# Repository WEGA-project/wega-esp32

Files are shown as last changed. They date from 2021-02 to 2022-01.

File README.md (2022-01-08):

# Важно !!!
**Данный репозиторий не актуален, используйте прошивку из [wegabox](https://github.com/WEGA-project/wegabox)**

*****

# WEGA-ESP32

Web Electronic Garden Automatic on ESP32 project.

Телеграмм канал проекта [WEGA-ESP32](https://t.me/esp32wega)

И так, что же такое **WEGA-ESP32(WEGA-Box)**

**WEGA-ESP32** это система контроля и мониторинга состояния гидропонной системы, куда входят следущие возможности
* Мониторинг `ЕС`
* Мониторинг `pH`
* Мониторинг `Температуры воздуха и раствора`(в баке и в корневой зоне)
* Мониторинг `Влажности воздуха`
* Мониторинг `Освещенности`
* Мониторинг `Уровня раствора`
* Управление корневым давление(на сколько это возможно)
* Контроль `ЕС` в рабочем баке(в разработке, дата релиза не известна)

Важно: **WEGA-ESP32(WEGA-Box)** не имеет смысла без [WEGA](https://github.com/WEGA-project/WEGA/wiki) части.

Так же **WEGA-ESP32** является важным звеном в [WEGA ecosystem](https://github.com/WEGA-project/WEGA-Mixer/blob/main/images/wega-ecosystem.jpg)

Содержание 
=================
<!--ts-->
* [Минимальные требования и знания](#what_to_know)
* [Схема подключения компонентов](#schema)
* [Что потребуется купить(ESP32, датчики, резисторы)](#what_to_buy)
<!-- * [PCB плата](#pcb) -->
* [Установка софта](#install)
  * [Arduino IDE](#arduino)
  * [Additional Boards Manager URLs](#boards_manager)
  * [Установка платы ESP32](#esp_board_install)
  * [Visual Studio Code configuration](#vscode)
* [Залив прошивки esp32wega](#esp_wega)
* [Компоненты для модуля измерения pH](#ph)
* [Корпуса для 3D печати](#3d)
* [Распиновка jack](#jack)
* [Калибровка EC](#ec)
* [Где искать помощь](#help)

<!--te-->

### Минимальные требования и знания

Для того, чтобы собрать этот миксер необходимо:

- Минимальные знания в электронике (знать что такое `+` или `GND`)
- Умение читать схему, да-да, именно читать, а не разглядывать и смотреть
- Знание, что такое паяльник и как с ним работать
- Понимание как соединить три проводка в одной точке
- Умение собирать компоненты по схеме
- Знать и уметь, как прошивать ардуину и вообще знать, что это такое
- Минимальные знания в программировании. Мы попытались минимизировать необходимость ковыряние в коде, но все же придется изменять некоторые значения, о которых речь пойдет ниже

Если, всего выше перечисленного или одного из выше перечисленного не знаешь, не умеешь, не понимаешь, найди человека, который соберет этот миксер за тебя.

## Схема подключения
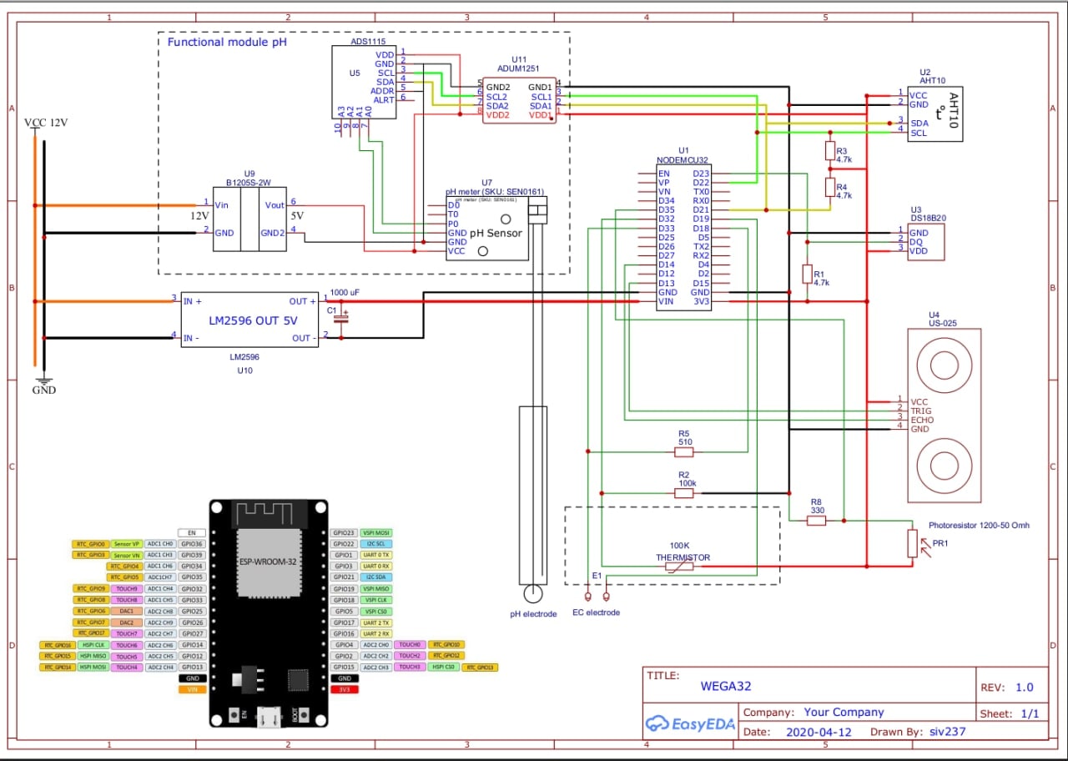
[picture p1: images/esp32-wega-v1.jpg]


## Компоненты для заказа
 1. Плата контроллера [ESP32-WROOM-32D или ESP32-WROOM-32U](https://www.aliexpress.com/wholesale?&SearchText=ESP32-WROOM-32D+ESP32-WROOM-32U+)
 1. Датчик температуры и влажности [ATH10](https://aliexpress.ru/wholesale?SearchText=AHT10). [Пример позиции](https://aliexpress.ru/item/4000961263862.html)
 1. Фоторезистор [GL5528](https://aliexpress.ru/wholesale?SearchText=GL5528) для измерения света. [Пример позиции](https://aliexpress.ru/item/1125719348.html)
 1. Датчик расстояния для измерения уровня [US-025](https://www.aliexpress.com/wholesale?&SearchText=Ultrasonic+Ranging+Module+US-025)
 1. Стабилизатор для питания контроллера [mini560 5V](https://aliexpress.ru/wholesale?&SearchText=mini560+step+down+5V)
 1. Терморезистор 100кОм для компенсации ЕС [NTC-MF52-100K](https://www.aliexpress.com/wholesale?&SearchText=Thermistor+Resistor+NTC-MF52-100K). [Пример позиции](https://aliexpress.ru/item/32865194243.html)
 1. Водонепроницаемый [ds18b20](https://www.aliexpress.com/wholesale?&SearchText=ds18b20+waterproof) датчик температуры корней. [Пример позиции](https://aliexpress.ru/item/32832225749.html)
 1. [Монтажная плата](https://aliexpress.ru/item/32546265487.html) или [такая](https://www.aliexpress.com/item/32512415633.html)
 1. Набор резисторов [Resistor Assorted Kit Set 10 -1M ](https://www.aliexpress.com/wholesale?&SearchText=Resistor+Assorted+Kit+Set+10+-1M+). [Пример позиции](https://www.aliexpress.com/item/1005002275520555.html)
 1. Провода ...

<!-- 

#### PCB плата
PCB плата находится в стадии активной разработки и тестирования, по этому если планируете заказать плату то иммейте ввиду, что нет ни какой гарантий,
что все будет работать как надо.

PCB плата [WEGA-ESP32](https://oshwlab.com/siv237/esp32wega4)

<a href="images/pcb-esp32-wega.png"><img src="images/pcb-esp32-wega.png" width="250"></a> 
-->

### Установка софта(Install software)

#### Arduino IDE
[Install Arduino IDE](https://www.arduino.cc/en/software)

Запускаем Arduino IDE, прописываем путь к `Additional Boards Manager URLs` для нашей ESP, устанавливаем нашу плату(board)

**Additional Boards Manager URLs**

File -> Preferences

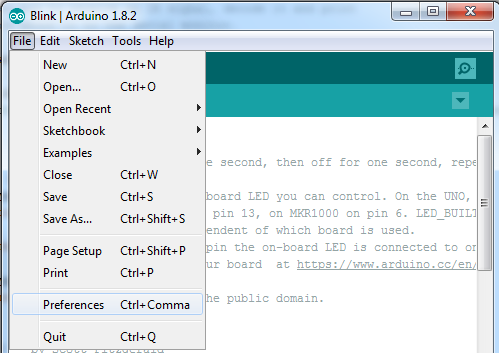
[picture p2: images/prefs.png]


И здесь нам надо изменить две вещи.

1. Необходимо указать расположение вашей папки с esp32 проектом/скетчами, где находятся файлы ардуины.

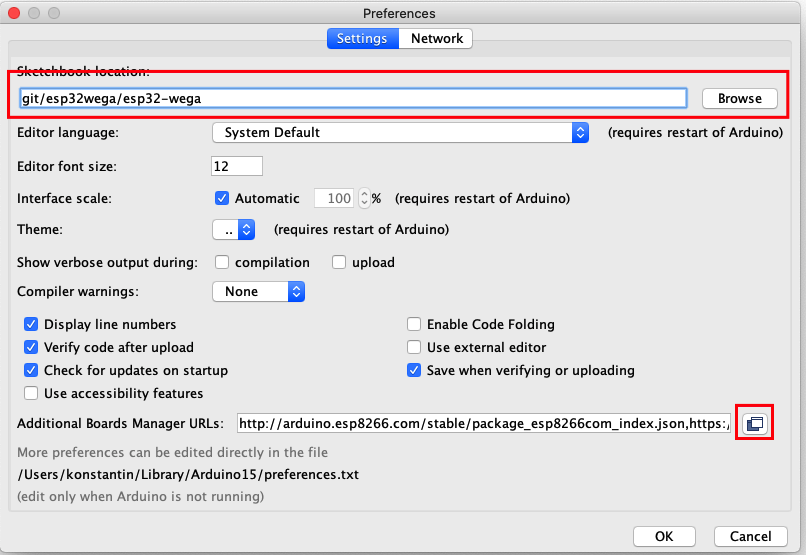
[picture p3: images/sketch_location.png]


2. Добавить ссылку на конфиг файл для установки esp32 платы. Для этого необходимо скопировать ссылку, которая приведена ниже и вставить ее в поле, которое откроется при нажатии кнопки, которая выделена красным квадратом

`https://raw.githubusercontent.com/espressif/arduino-esp32/gh-pages/package_esp32_dev_index.json`

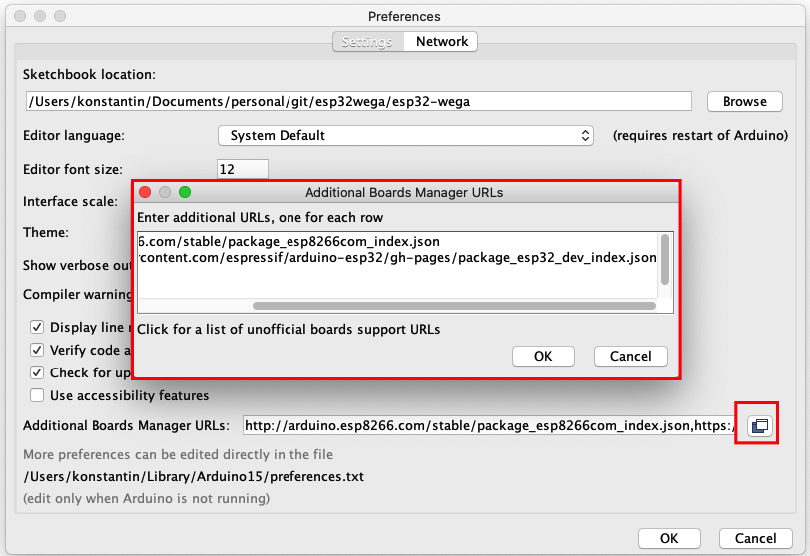
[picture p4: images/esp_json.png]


**Установка платы ESP32**

Tools -> Board -> Board managers

Ищем `ESP32`, выбираем версию 1.0.6 и нажимаем `intstall`

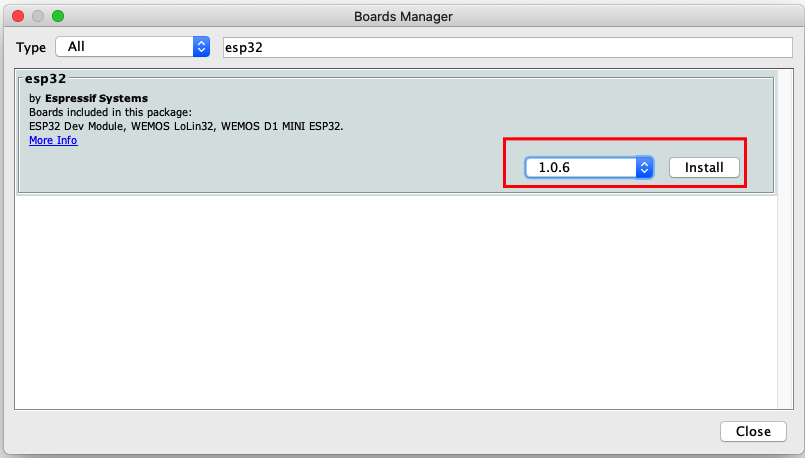
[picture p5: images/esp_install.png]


Выбираем правильную плату ESP

`Tools -> boards manager -> ESP32 Arduino -> NodeMCU-32S`

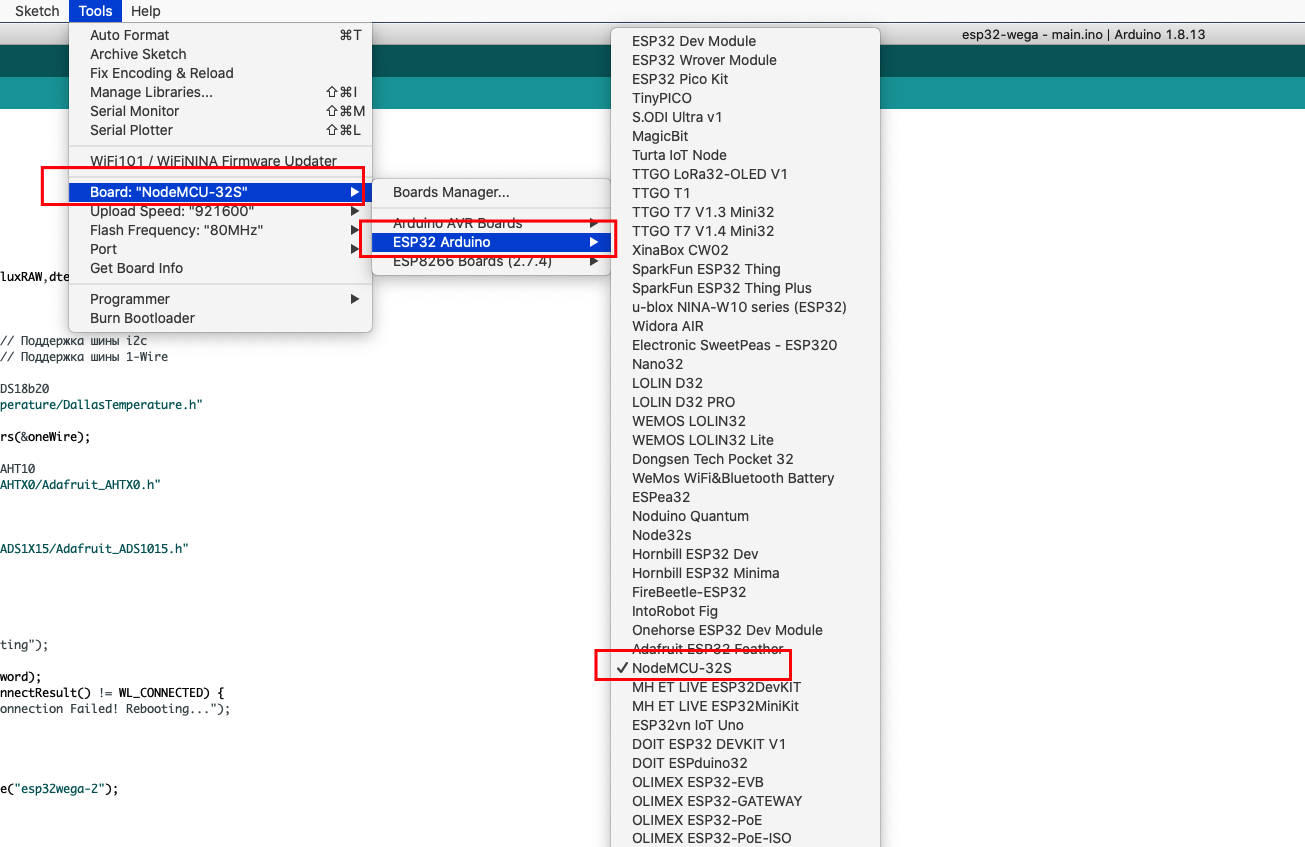
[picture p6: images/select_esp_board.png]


Выбираем `Upload Speed` `115200` или меньше.



Изначальное конфигурирование Arduino IDE закончено

Для поддержки платы в Windows необходимо установить драйвер USB http://www.wch.cn/downloads/CH341SER_ZIP.html

Вы можете пропустить следующий шаг если вы собираетесь использовать vscode как основной IDE

#### Visual Studio Code configuration
<details>
<p>

Если вы планируете использовать vscode как основную IDE для работы с файлами ардуины вам потребуется установить [arduino plugin](https://marketplace.visualstudio.com/items?itemName=vsciot-vscode.vscode-arduino) и сконфигурировать его для работы с вашей платой.

[Здесь видео пример как это сделать](https://www.youtube.com/watch?v=FnEvJXpxxNM)
</p>
</details>

### Залив прошивки WEGA-ESP32

- Открываем файл прошивки из папки `esp32wega/esp32-wega/esp32-wega.ino`
- Обновляем `ssid` - имя вашей сети и `password` - пароль для вашего WiFi.
- Обновляем `wegaapi` - необходимо вставить IP address WEGA сервера
- Обновляем `wegaauth` - необходимо сгенерировать токен для авторизации запросов через API
- Обновляем `wegadb` - необходимо указать имя базы данных

```bash
const char* ssid = "YOUR_WIFI_NETWORK_NAME";
const char* password = "YOUR_WIFI_PASSWORD";
String wegaapi  = "http://192.168.1.XX/wega-api/esp32wega.php"; 
String wegaauth = "adab637320e5c47624cdd15169276981";              
String wegadb   = "esp32wega";
```

- Сохраняем код
- Подключаем `USB` кабель к `esp` плате и выбираем `Tools -> Port` и выбираем ваш порт консольного подключения

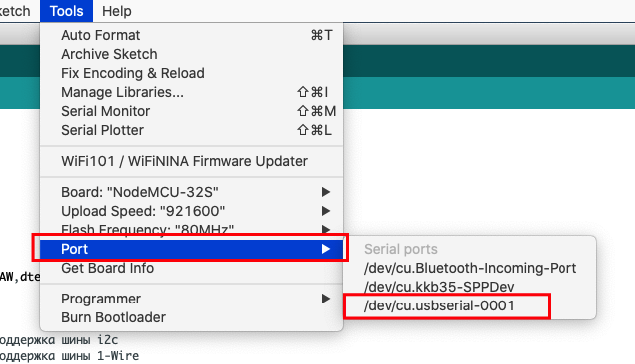
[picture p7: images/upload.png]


- Нажимаем upload/загрузить

Как только код/скетч будет загружен на плату и произойдет перезагрузка, можно увидеть адрес `esp32-wega`, для этого необходимо открыть меню `Tools -> Port`

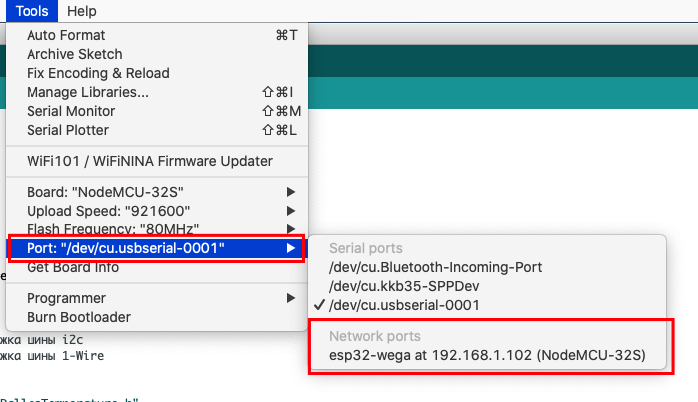
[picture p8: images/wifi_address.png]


Теперь можно попробовать зайти на этот адрес через браузер, вы увидете, страницу с данными

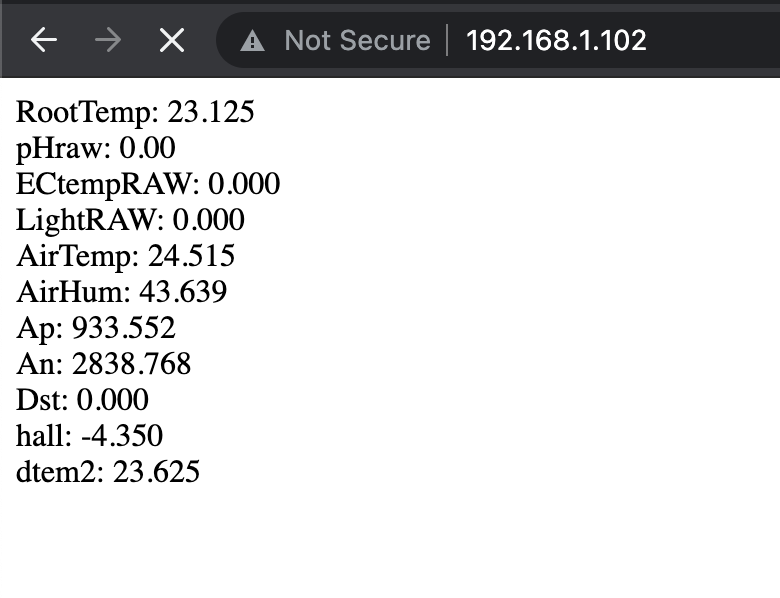
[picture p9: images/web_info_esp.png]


Ну все, код залит, веб сервер работает.

## Компоненты для модуля измерения pH
 1. АЦП ADS1115 https://aliexpress.ru/item/32954034047.html
 1. Изолятор питания B1205S-2W https://aliexpress.ru/item/1005001291619304.html
 1. Изолятор шины i2c ADUM1251 https://aliexpress.ru/item/33052971531.html
 1. Плата для распайки изолятора i2c https://aliexpress.ru/item/1728075292.html
 1. Шилд pH https://aliexpress.ru/item/1005001672420703.html
 1. Набор для калибровки pH https://aliexpress.ru/item/33025867435.html

## Корпуса элементов для 3D печати
#### Изготовление электрода ЕС
[Здесь](https://t.me/esp32wega/87) можно видеть процесс изготовления EC электрода из напечатанных элементов на 3D принтере. 

Файлы для печати можно найти [здесь](./images/ec)

#### Изготовление корпуса для контроллера
[Здесь](https://t.me/esp32wega/2850) можно видеть процесс изготовления `WEGA-Box` из напечатанных элементов на 3D принтере.

Файлы для печати корпус для контроллера(WEGA-Box) можно найти [здесь](./images/box)

#### Изготовление корпуса для датчика контроля уровня раствора
[Здесь](https://t.me/esp32wega/2363) можно видеть процесс изготовления корпуса датчика уровня раствора из напечатанных элементов на 3D принтере.

Файлы для печати корпус для датчика уровня можно найти [здесь](./images/us)

#### Изготовление корпуса для датчика AHT10
[Здесь](https://t.me/esp32wega/2352) можно видеть процесс изготовления корпуса датчика измерения температуры и влажности воздуха из напечатанных элементов на 3D принтере.

Файлы для печати корпус для датчика AHT10 можно найти [здесь](./images/aht)

#### Распиновка jack коннекторов
[Здесь](https://github.com/WEGA-project/WEGA-ESP32/blob/master/images/jack.jpeg) можно посмотреть распиновку jack коннекторов для разных компонентов. Таких как ЕС, pH, AHT10 и так далее. 

## Калибровка EC
Для калибровки наиболее удобно использовать аптечный раствор кальция хлорида(Хлорида Кальция) шестиводного. 
Жидкий в ампулах 100 г/л на 5 или 10 мл.
Можно приготовить три калибровочных раствора 1, 2 и 5 ампул вылить в 500мл бутылку и долить воды до отметки 500мл (если ампула 10мл то в литровой бутылке и долить до литра) дистиллята с ЕС 0.01.

#### Изготовление калибровочных растворов
 * 1 ампула ЕС = 1.114 мсм/см
 * 2 апулы ЕС = 2.132 мсм/см
 * 3 апулы ЕС = 3.107 мсм/см
 * 4 апулы ЕС = 4.057 мсм/см
 * 5 ампул ЕС = 4.988 мсм/см
 * 6 ампул ЕС = 5.909 мсм/см

### Где искать помощь

Если у вас все еще есть вопросы по настройке, заливке и гонфигурированни этого дозера/миксера, 
то их всегда можно задать в официальном телеграмм канале [WEGA-ESP32](https://t.me/esp32wega)

**!!! ВАЖНО !!!**

Ответы на вопросы, а что такое плюс или GND, а как быть с проводами и так далее в телеграмм канале дававться не будут.

Смотри [Минимальные требования и знания](#what_to_know)

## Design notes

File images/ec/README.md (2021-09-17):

## Изготовление электрода ЕС

3D корпус ЕС метра

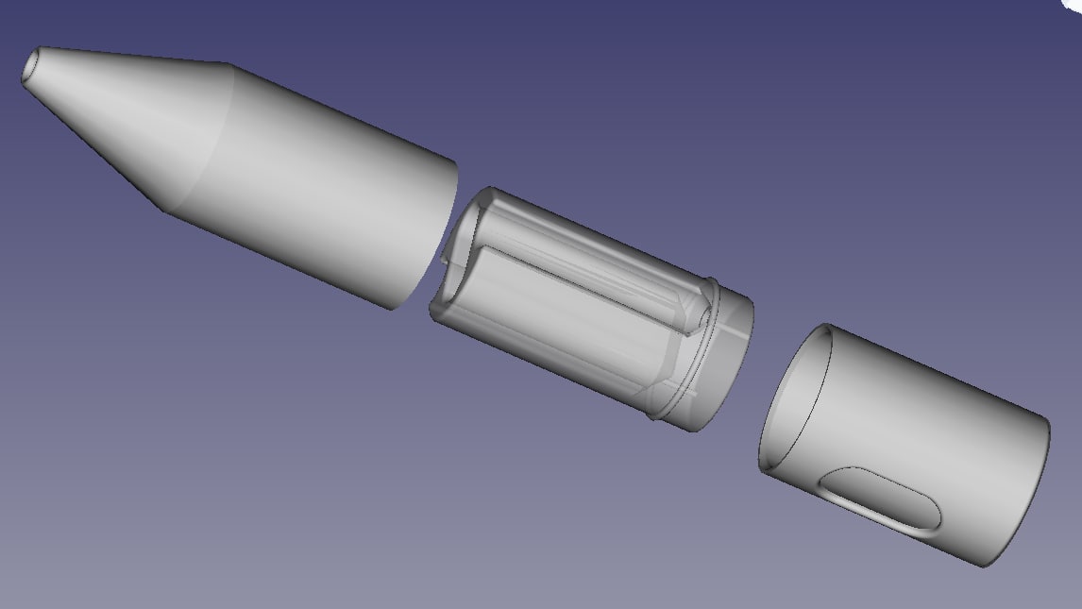
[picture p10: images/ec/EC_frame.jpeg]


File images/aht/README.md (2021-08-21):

## Изготовление корпуса для датчика температуры и влажности воздуха

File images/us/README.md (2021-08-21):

## Изготовление корпуса для датчика уровня раствора

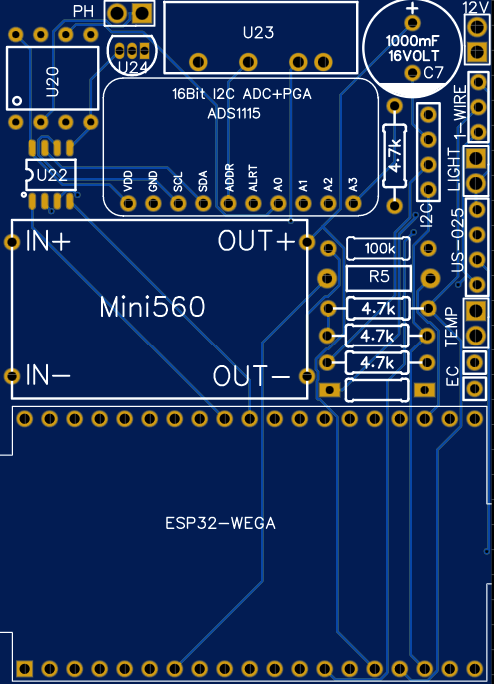
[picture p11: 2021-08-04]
images/pcb-esp32-wega.png

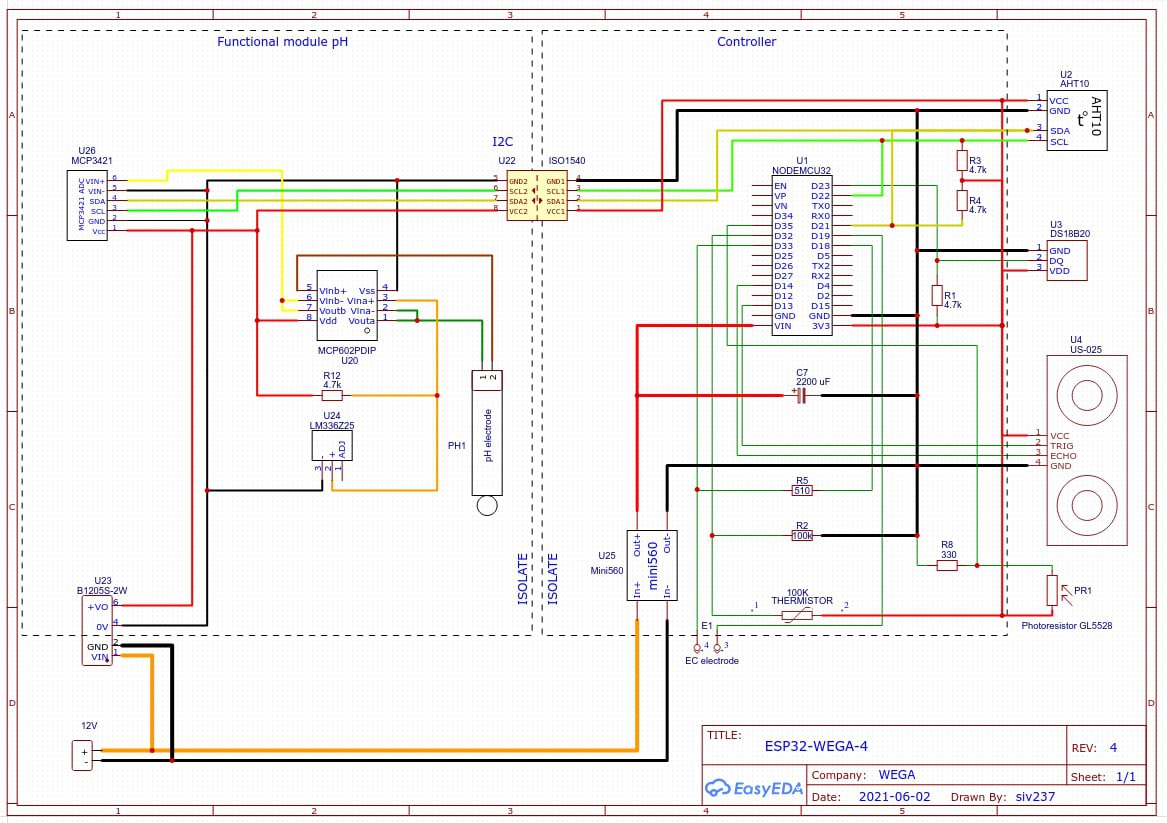
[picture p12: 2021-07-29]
images/esp32-wega-v4.jpg

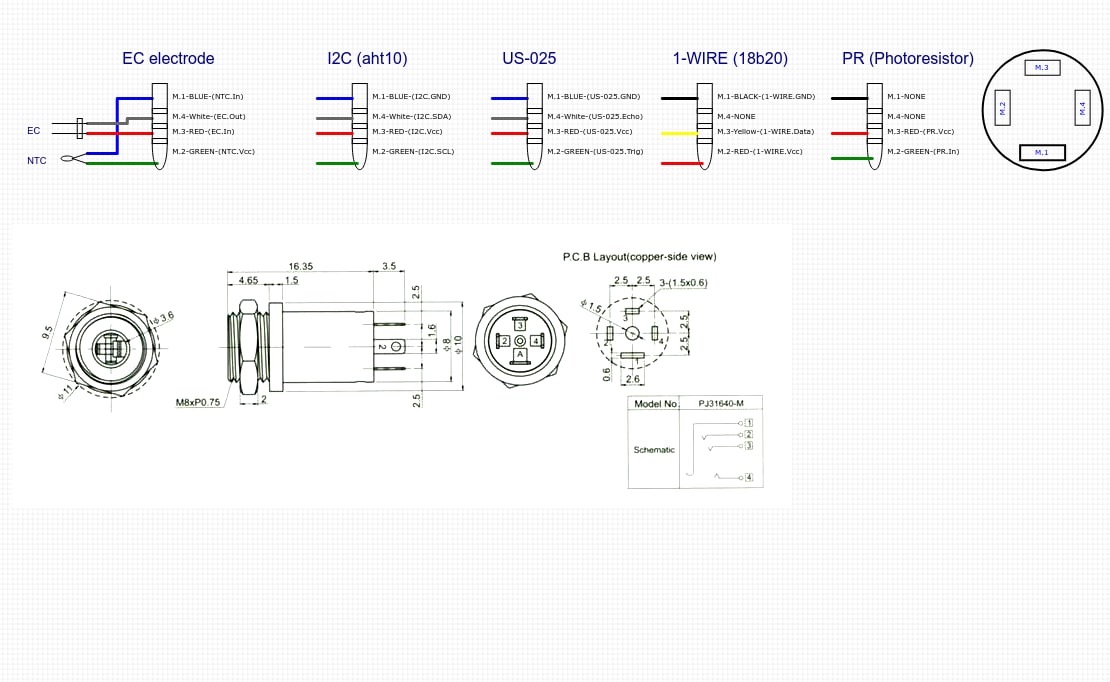
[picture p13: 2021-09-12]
images/jack.jpeg

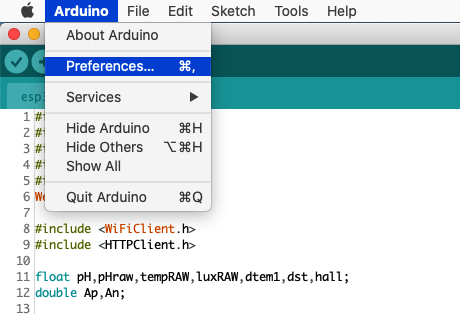
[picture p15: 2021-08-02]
images/pref.png

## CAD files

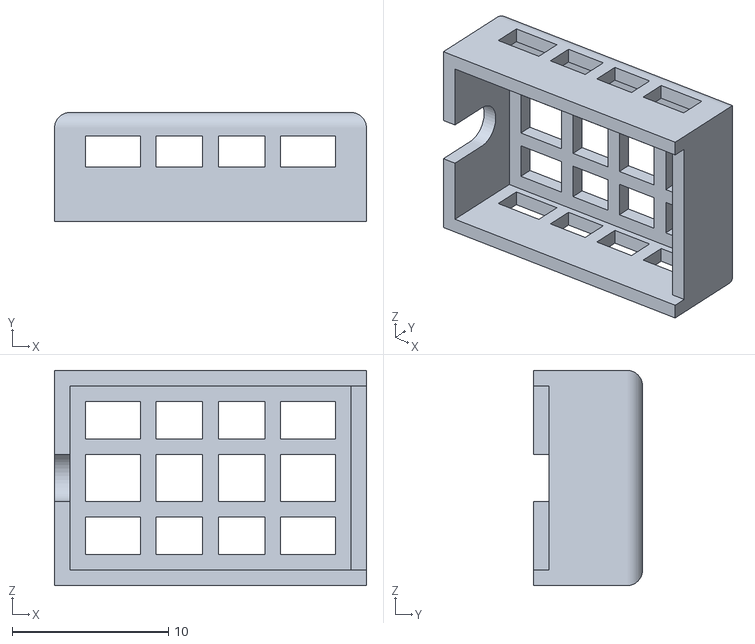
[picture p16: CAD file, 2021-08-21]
images/aht/top_AHT10.STL
20.0 x 7.00 x 13.8

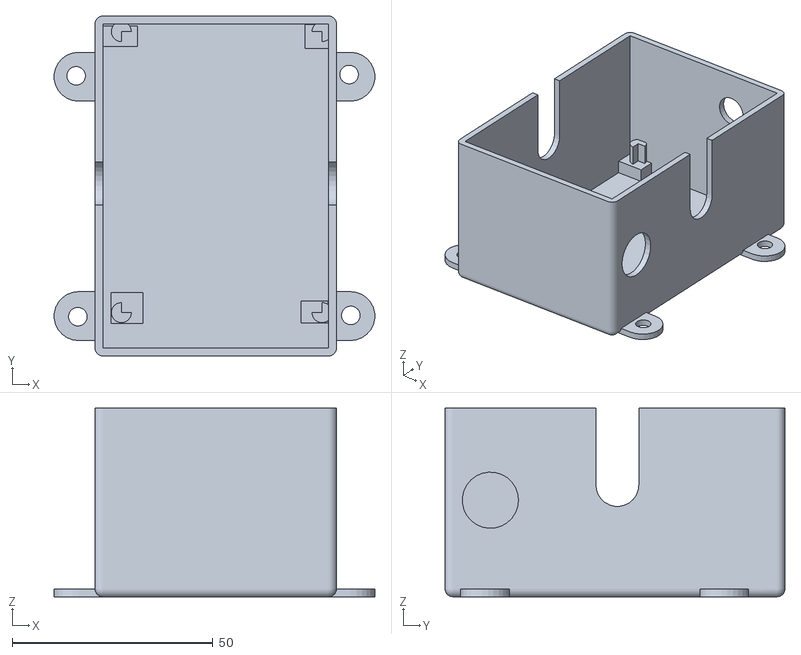
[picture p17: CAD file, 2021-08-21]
images/box/esp32wega-korpus.stl
79.9 x 84.7 x 47.0

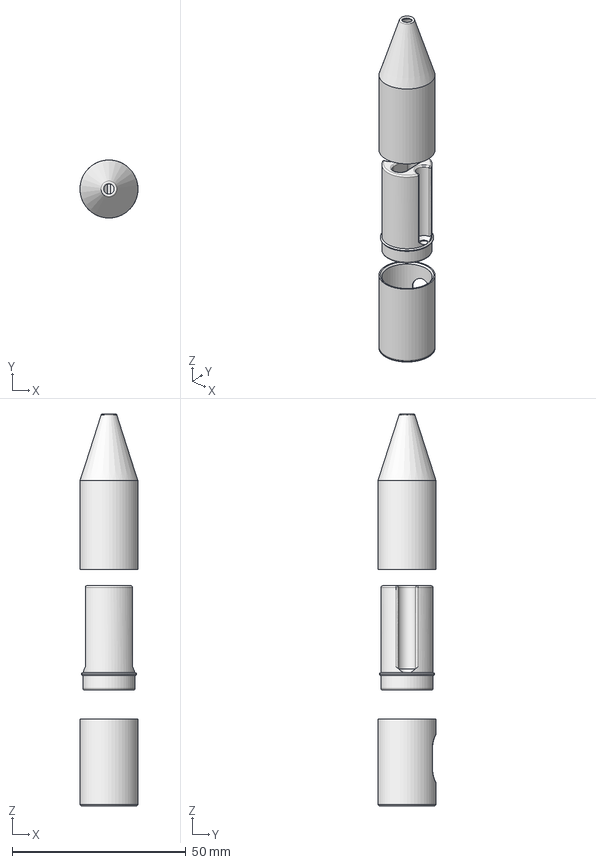
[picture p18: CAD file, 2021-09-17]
images/ec/es3.FCStd
16.7 x 16.7 x 112.8 mm
korpus
guard
che

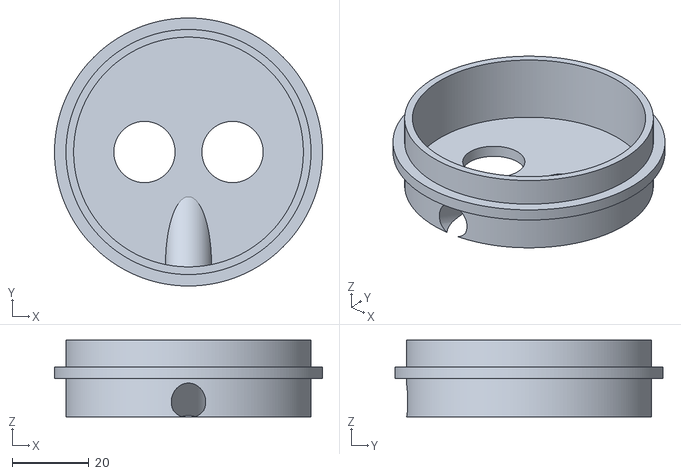
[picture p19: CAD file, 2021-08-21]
images/us/probka2k-uz.stl
70.0 x 70.0 x 20.0

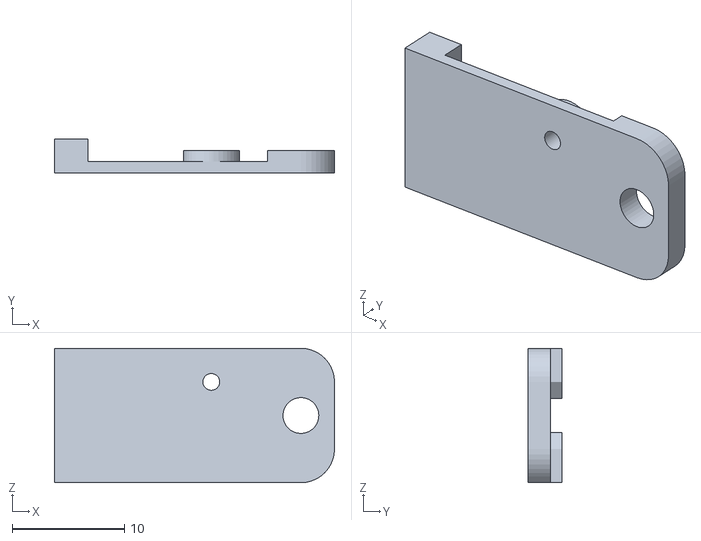
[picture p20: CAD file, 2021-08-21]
images/aht/base_AHT10.STL
25.0 x 3.00 x 12.0

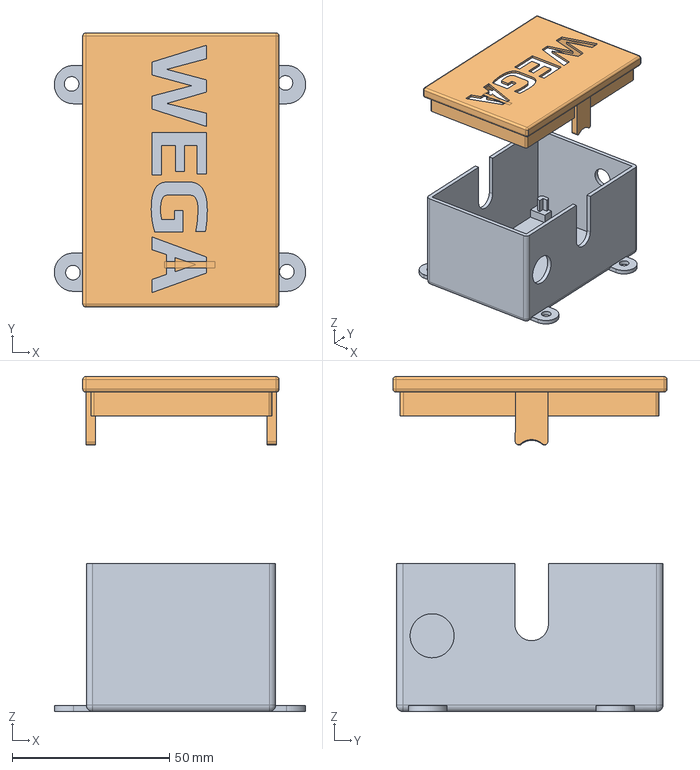
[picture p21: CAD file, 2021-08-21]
images/box/box2.FCStd
80.0 x 87.2 x 106.5 mm
Корпус

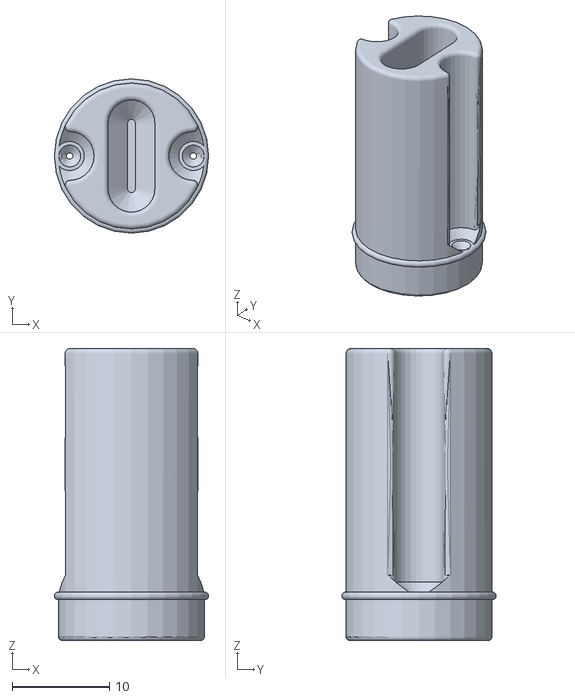
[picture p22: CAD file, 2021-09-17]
images/ec/ec3-korp.stl
15.9 x 15.9 x 30.0

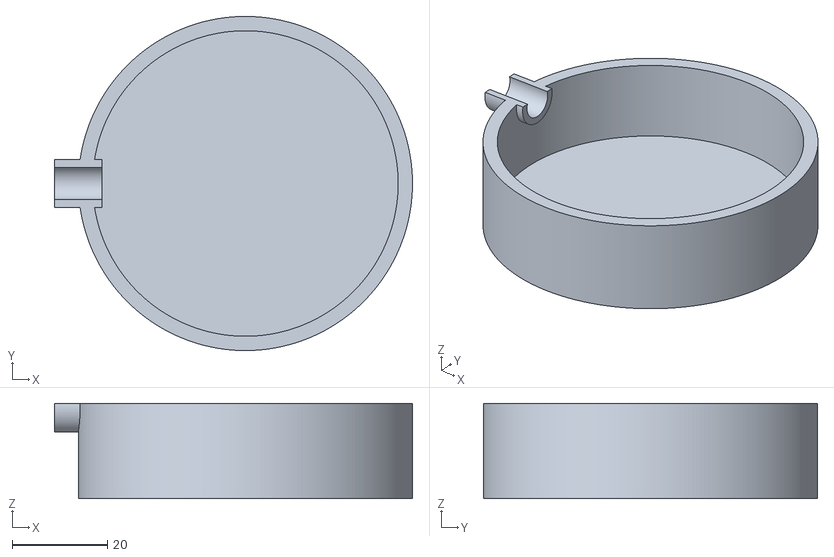
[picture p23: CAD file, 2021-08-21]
images/us/probka2k-verh-uz.stl
75.0 x 70.0 x 20.0

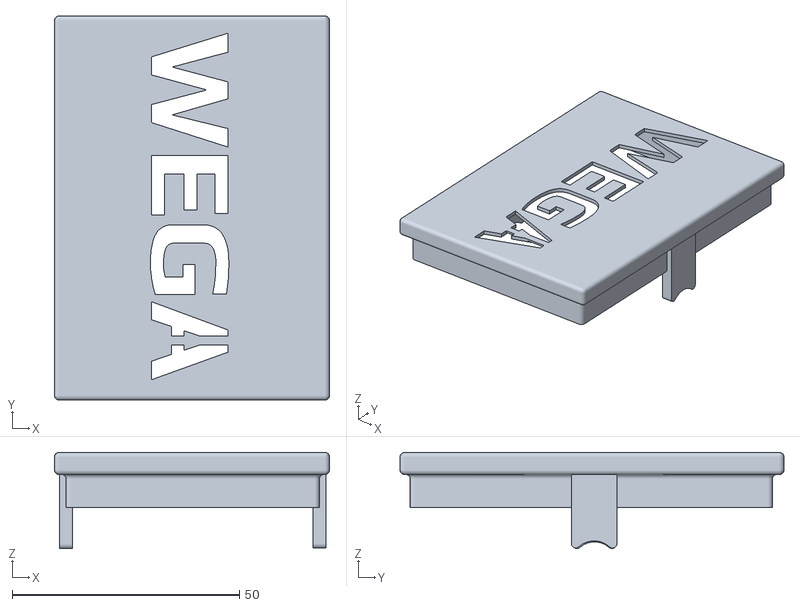
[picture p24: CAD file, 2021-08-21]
images/box/esp33up.stl
60.6 x 84.6 x 21.2

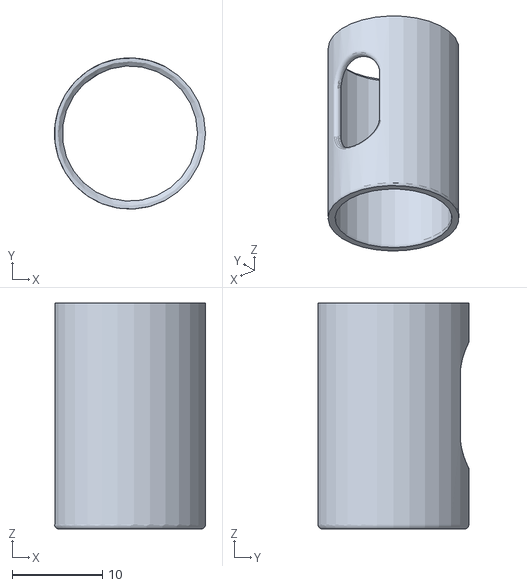
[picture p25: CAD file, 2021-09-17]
images/ec/ec3-guard.stl
16.7 x 16.7 x 25.0

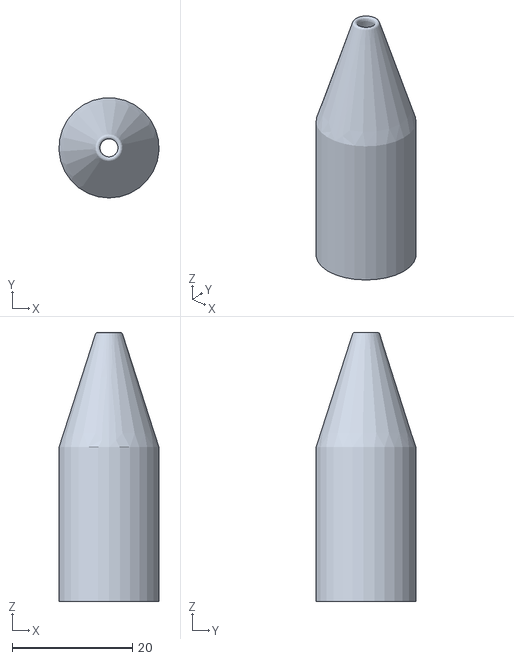
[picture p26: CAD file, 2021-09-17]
images/ec/ec3-cheshol.stl
16.7 x 16.6 x 44.8

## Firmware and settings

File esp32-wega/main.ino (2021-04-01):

#include <WiFi.h>
#include <ESPmDNS.h>
#include <WiFiUdp.h>
#include <ArduinoOTA.h>
#include <WebServer.h>
WebServer server(80);

#include <WiFiClient.h>
#include <HTTPClient.h>

float pH,pHraw,tempRAW,luxRAW,dtem1,dst,hall;
double Ap,An;


#include <Wire.h>      // Поддержка шины i2c
#include <OneWire.h>   // Поддержка шины 1-Wire

// Библиотека работы с DS18b20
#include "src/DallasTemperature/DallasTemperature.h"
OneWire oneWire(23);
DallasTemperature sensors(&oneWire);

// Библиотека работы с AHT10
#include "src/Adafruit_AHTX0/Adafruit_AHTX0.h"
Adafruit_AHTX0 aht;

// ADS1115 for pH
#include "src/Adafruit_ADS1X15/Adafruit_ADS1015.h"
Adafruit_ADS1115 ads;


void setup() {
  Serial.begin(9600);
  //Serial.println("Booting");
  WiFi.mode(WIFI_STA);
  WiFi.begin(ssid, password);
  while (WiFi.waitForConnectResult() != WL_CONNECTED) {
    //Serial.println("Connection Failed! Rebooting...");
    delay(5000);
    ESP.restart();
  }

  ArduinoOTA.setHostname("esp32wega-2");

  ArduinoOTA
    .onStart([]() {
      String type;
      if (ArduinoOTA.getCommand() == U_FLASH)
        type = "sketch";
      else // U_SPIFFS
        type = "filesystem";

      // NOTE: if updating SPIFFS this would be the place to unmount SPIFFS using SPIFFS.end()
      Serial.println("Start updating " + type);
    })
    .onEnd([]() {
      Serial.println("\nEnd");
    })
    .onProgress([](unsigned int progress, unsigned int total) {
      Serial.printf("Progress: %u%%\r", (progress / (total / 100)));
    })
    .onError([](ota_error_t error) {
      Serial.printf("Error[%u]: ", error);
      if (error == OTA_AUTH_ERROR) Serial.println("Auth Failed");
      else if (error == OTA_BEGIN_ERROR) Serial.println("Begin Failed");
      else if (error == OTA_CONNECT_ERROR) Serial.println("Connect Failed");
      else if (error == OTA_RECEIVE_ERROR) Serial.println("Receive Failed");
      else if (error == OTA_END_ERROR) Serial.println("End Failed");
    });

  ArduinoOTA.begin();

  Serial.println("Ready");
  Serial.print("IP address: ");
  Serial.println(WiFi.localIP());

  MDNS.begin("esp32-wega");
  MDNS.addService("http", "tcp", 80);
  server.on("/", handleRoot);
  server.begin();

  Wire.begin();
  ads.begin(); 
  //ads.setGain(GAIN_TWOTHIRDS);
  //ads.setGain(GAIN_SIXTEEN);
  ads.setGain(GAIN_TWOTHIRDS);  // 2/3x gain +/- 6.144V  1 bit = 3mV      0.1875mV (default) 

// AHT10 > temperature and humidity
aht.begin();

//BS18B20 > temperature
sensors.begin();
delay(300);
sensors.requestTemperatures();
sensors.getTempCByIndex(0);
}

void loop() {
    server.handleClient();
    ArduinoOTA.handle();


// AHT10 > temperature and humidity
  sensors_event_t humidity, temp;
  aht.getEvent(&humidity, &temp);

// Termistor for EC (port, averaging counter) > RAW
tempRAW=AnalogReadMid(32,500000);

// EC sensor
// Electrode (d-port 1,d-port 2, a-port, averaging counter) > RAW
ec(18,19,33,80000);



// Photoresistor for Luxmetter 
luxRAW=AnalogReadMid(35,10000);


// Level ultrasound (echo, trig, temp, averaging counter) > cm 
dst=us(13,14,25,60);

//pH RAW over ADS1115 > RAW
pHraw = adsdiff01(5000); 

// Integrated Hall Sensor read
hall=hallmid(100);

//BS18B20 > temperature
 sensors.requestTemperatures();
 dtem1=sensors.getTempCByIndex(0); 
 
// Sending to WEGA-API 
WiFiClient client;
HTTPClient http;

String httpstr=wegaapi;
httpstr +=  "?db=" + wegadb;
httpstr +=  "&auth=" + wegaauth;
httpstr +=  "&pHraw=" + fFTS(pHraw,2);
httpstr +=  "&ECtempRAW=" + fFTS(tempRAW,3);
httpstr +=  "&LightRAW=" + fFTS(luxRAW,3);
httpstr +=  "&RootTemp=" + fFTS(dtem1,3);
httpstr +=  "&AirTemp=" +fFTS(temp.temperature, 3);
httpstr +=  "&AirHum=" +fFTS(humidity.relative_humidity, 3);
httpstr +=  "&Ap=" +fFTS(Ap, 3);
httpstr +=  "&An=" +fFTS(An, 3);
httpstr +=  "&Dst=" +fFTS(dst, 3);
httpstr +=  "&hall=" +fFTS(hall, 3);


http.begin(client, httpstr);
http.GET();
http.end();


  if (WiFi.status() != WL_CONNECTED) {
    WiFi.disconnect(true);
    WiFi.begin(ssid, password);  }

}


void handleRoot() {
sensors.requestTemperatures();

  sensors_event_t humidity, temp;
  aht.getEvent(&humidity, &temp);// populate temp and humidity objects with fresh data

String httpstr="<meta http-equiv='refresh' content='10'>";
       httpstr +=  "RootTemp: " + fFTS(dtem1,3) + "<br>";
       httpstr +=  "pHraw: " + fFTS(pHraw,2) + "<br>";
       httpstr +=  "ECtempRAW: " + fFTS(tempRAW,3)+ "<br>";
       httpstr +=  "LightRAW: " +fFTS(luxRAW, 3) + "<br>";
       httpstr +=  "AirTemp: " +fFTS(temp.temperature, 3) + "<br>";
       httpstr +=  "AirHum: " +fFTS(humidity.relative_humidity, 3) + "<br>";
       httpstr +=  "Ap: " +fFTS(Ap, 3) + "<br>";
       httpstr +=  "An: " +fFTS(An, 3) + "<br>";
       httpstr +=  "Dst: " +fFTS(dst, 3) + "<br>";
       httpstr +=  "hall: " +fFTS(hall, 3) + "<br>";

       
server.send(200, "text/html",  httpstr);

}

// Функция преобразования чисел с плавающей запятой в текст с округлением
String fFTS(float x, byte precision) {
  char tmp[50];
  dtostrf(x, 0, precision, tmp);
  return String(tmp);
}

// Функция усреднения значений измерения напряжения на ADS1115 между портами 0 и 1
float adsdiff01(long count) {
    ArduinoOTA.handle();

  long n=0;
  double sensorValue=0;
  while ( n< count){
    n++;
        server.handleClient();
    ArduinoOTA.handle();
  sensorValue = (ads.readADC_Differential_0_1())+sensorValue;
 }
 return sensorValue/n;

}

// Функция измерения датчиком холла
float hallmid(long count) {
    ArduinoOTA.handle();

  long n=0;
  double sensorValue=0;
  while ( n< count){
    n++;
        server.handleClient();
    ArduinoOTA.handle();
  sensorValue = hallRead()+sensorValue;
 }
 return sensorValue/n;
}



// Функция усреднения измерения аналогово порта
float AnalogReadMid(int port, long count) {
    server.handleClient();
    ArduinoOTA.handle();
    pinMode(port, OUTPUT);
    digitalWrite(port, HIGH);
    delayMicroseconds(1000);
    pinMode(port, INPUT);
    delayMicroseconds(1000);
  long n=0;
  double sensorValue=0;
  while ( n< count){
    n++;
        server.handleClient();
    ArduinoOTA.handle();
    
  
  sensorValue = (analogRead(port))+sensorValue;
 
 }
 return sensorValue/n;

}

// Функция измерения аналогового знаения ЕС
void ec(char d1,  char d2, char a0, long l) {

    Ap=0;
    An=0;
  double n = 0;

    //pinMode(a0, INPUT_PULLUP);
    pinMode(a0, INPUT);
    pinMode(d1, OUTPUT);
    pinMode(d2, OUTPUT);

  while (n < l) {

    ArduinoOTA.handle(); 
    
    n++;

    digitalWrite(d1, HIGH);
    delayMicroseconds(1);
    Ap = analogRead(a0)+Ap; 
    digitalWrite(d1, LOW); 
         
    digitalWrite(d2, HIGH);
    delayMicroseconds(1);
    An = analogRead(a0)+An; 
    digitalWrite(d2, LOW); 

   

  }
    //delay(300);
    pinMode(d1, INPUT);
    pinMode(d2, INPUT);
    pinMode(a0, INPUT);


    
    Ap=Ap/n;
    An=An/n;
    
    ArduinoOTA.handle();

}

// Функция прямого опроса ультразвукового датчика возврат в микросекундах эха
float us(int trg, int ech, float temp, long cnt) {
   long count=0;
 long microssum=0;
 while (count < cnt) {
  count++;
    ArduinoOTA.handle();
       
    pinMode(trg, OUTPUT );
    pinMode(ech, INPUT);

    digitalWrite(trg,1);
    delayMicroseconds(10);
    digitalWrite(trg,0);


    long n=0;
    long limit=100000;
    
    long startmic,endmicros;
    while (n<limit){
      n++;
    if(digitalRead(ech) == 1)  
      {
      startmic=micros();
      long z=0;
      while (digitalRead(ech) == 1 and z<20000) {
        z++;
        endmicros=micros();
        }
        n=limit;
        delay(200);
      } 

    }

  microssum=microssum+(endmicros-startmic);
      
 }
 
 float vSound=20.046796*sqrt(273.15+25);
 return (vSound/10000)*((float(microssum)/count)/2); // В сантиметрах
 //return (float(microssum)/count);  // В миллисекундах
}

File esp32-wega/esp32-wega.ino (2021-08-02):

/////////////////////////////////////////////////////////////////////////////////////////////////////////////
// Устройство для измерений состояния раствора гидропоники ESP32WEGA подробности в https://t.me/esp32wega  //
// Является частью проекта WEGA https://t.me/WEGA_project                                                  //
/////////////////////////////////////////////////////////////////////////////////////////////////////////////

// Параметры подключения к WiFi
// Имя WiFi точки доступа
const char* ssid = "SSID";

// Пароль к точке доступа
const char* password = "PASSWORD";

// Параметры подключения к WEGA-API
// Адрес wega-api где ADDRESS адрес установленного сервера WEGA-API https://github.com/WEGA-project/WEGA/wiki/install
String wegaapi  = "http://WEGA_IP_ADDRESS/wega-api/esp32wega.php"; 

// Код доступа к api смотри файл /var/WEGA/wega-api/esp32wega.php
// Ключ тут: $auth="adab637320e5c47624cdd15169276981";
// Внимание, при размещении сервера WEGA в открытом интернете ключ лучше сменить!
String wegaauth = "adab637320e5c47624cdd15169276981"; 

// Имя базы данных - уникальное имя для устройства. База будет создана автоматически.
// каждому устройству должна быть назначена своя отдельная база!             
String wegadb   = "esp32wega";

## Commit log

2020-02-24 Первая заливка
2020-03-03 Добавлена поддержка AM2320
2020-04-11 Добавлен опрос ЕС
2020-12-16 Причесан код, добавлены коментарии. Добавления касаемые авторизации доступа к wega-api для передачи данных
2021-02-17 Обновлена прошивка для новой схемы с aht10
2021-02-26 Библиотеки включены в скетч. Исправлена проблема с отваливанием WiFi при перезапуске точки доступа.
    [Alarm.pde, AlarmHandler.pde, Multibus_simple.ino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]
2021-03-21 Исправлена ошибка, из-за которой при каждом старте системы датчик температуры корней 18b20 выдавал разово 85 градусов.
    [main.ino]
2021-03-27 Расширена форма текущих показаний, теперь видны статусы и можно смотреть быстро конкретный график
2021-04-01 Добавлен считыватель датчика холла, еще раз исправлена проблема 85 градусов на 18b20 и увеличена точность работы терморезистора, добавлен режим снижающий самонагрев терморезистора за счет зануления т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
    [main.ino]
2021-05-25 файл расчета терморезистора
2021-05-25 обновлен файл расчета терморезистора
2021-07-29 Added: esp32-wega schema
2021-08-04 PCB img
2021-08-08 Removed PCB part
    PCB is not tested yet. Will be updated in the future.
2021-08-21 Added: 3D printing elements
    [box2.FCStd, ec3-c.stl, ec3-k.stl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]
2021-08-21 Added: 3D AHT10 elements
    [base_AHT10.STL, top_AHT10.STL]
2021-09-12 Распиновка подключения джек коннекторов
2021-09-12 Распиновка jack
2021-09-17 New EC meter frame
    [ec3-cheshol.stl, ec3-guard.stl, ec3-korp.stl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]
2021-09-17 added ec frame picture
